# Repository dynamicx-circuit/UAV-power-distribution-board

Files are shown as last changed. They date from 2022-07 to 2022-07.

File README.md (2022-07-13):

#### 这是一个通过24V电池二串三并提高到48V的分电板
该版本采用LM5050-2作为理想二极管控制器以防止电池间互充。
#### 现存问题
1.现在无人机使用的为第5版，板上的48V降24V并未投入使用。<br>
2.使用该板时应注意电池的电压尽量保持一致，持续工作时间应小于10min，以避免电池过热。<br>
3.实机测试时MOS管需安装散热片并配合散热风扇使用，以免MOS热击穿。<br>
4.若要进行实机测试，***一定要在48V输出和GDN之间接入气体放电管***，并且***切记不可在48V输出和GND之间接入压敏电阻***。（接入压敏电阻后在限流情况下，输出电压较输入电压低2V~3V，未限流情况下，压敏电阻会在接GND的一侧炸裂，目前原因不明。）<br>
5.尽量使用高温锡焊接。<br>
6.该版本的地回路并未进行开窗，输出地较电池负极端距离较远。<br>

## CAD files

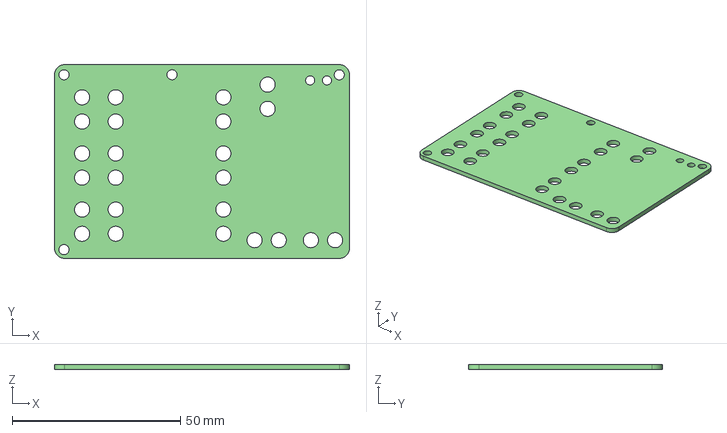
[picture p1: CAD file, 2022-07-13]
无人机分电板_V5.step
87.8 x 57.7 x 1.60 mm

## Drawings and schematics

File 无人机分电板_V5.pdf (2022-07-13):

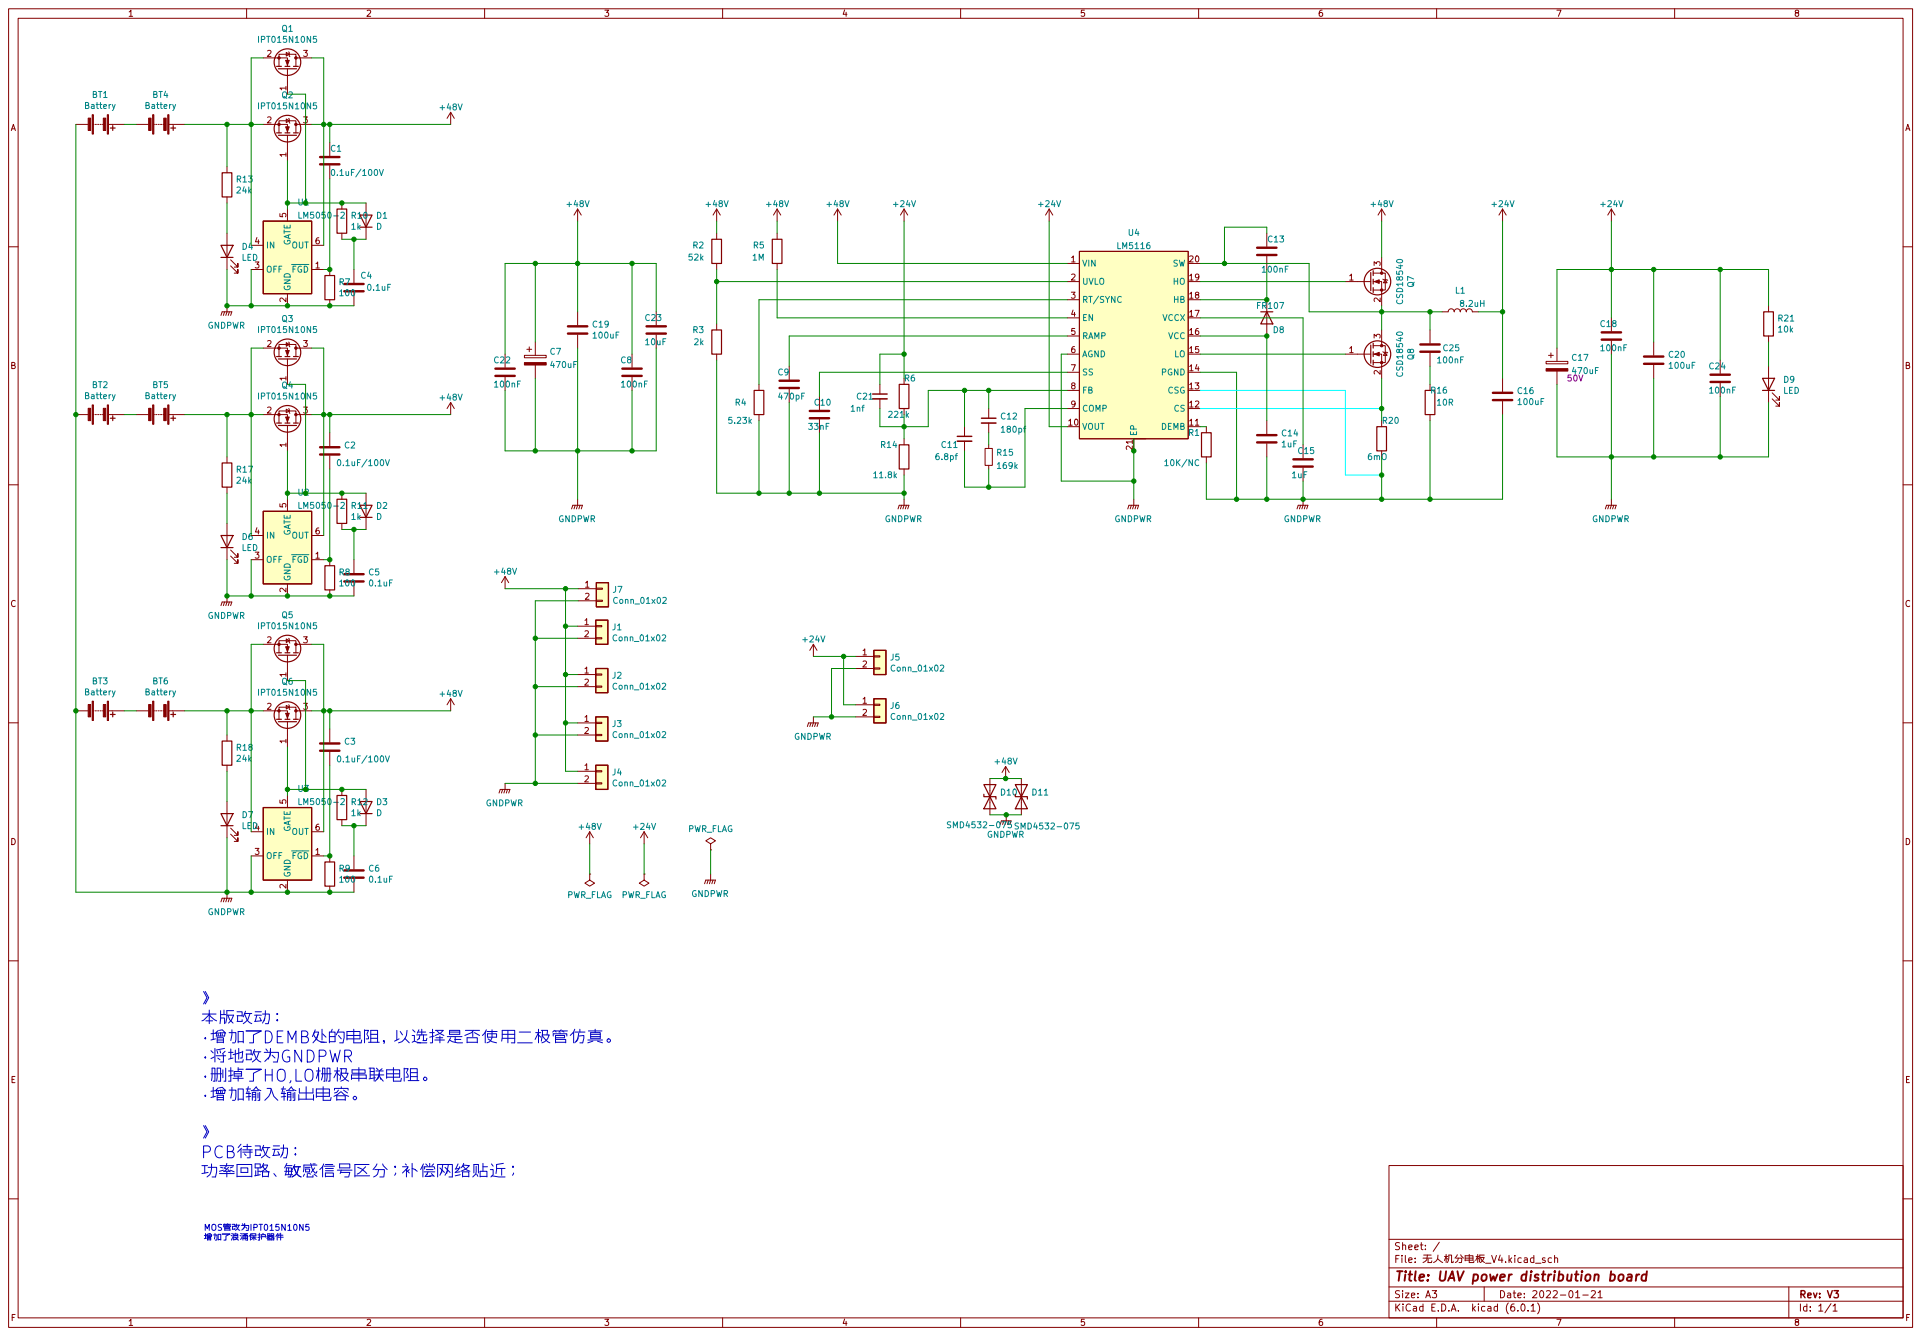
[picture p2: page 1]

þÿg,rHe9R¨ÿ
þÿ·XžR N†DEMBYv„u5–;ÿNå• béf/T&O•u(NŒg•{¡Nÿw0-
þÿ·XžR •“Qe•“Qúu5[¹0-

þÿRŸs‡VÞ•ï0eOaOáS÷S:RÿˆeP••Q~Ü•4•Ñÿ

þÿFile: eàNºg:Ru5g•_V4.kicad_sch Sheet: /
Id: 1/1 Title: UAV power distribution board

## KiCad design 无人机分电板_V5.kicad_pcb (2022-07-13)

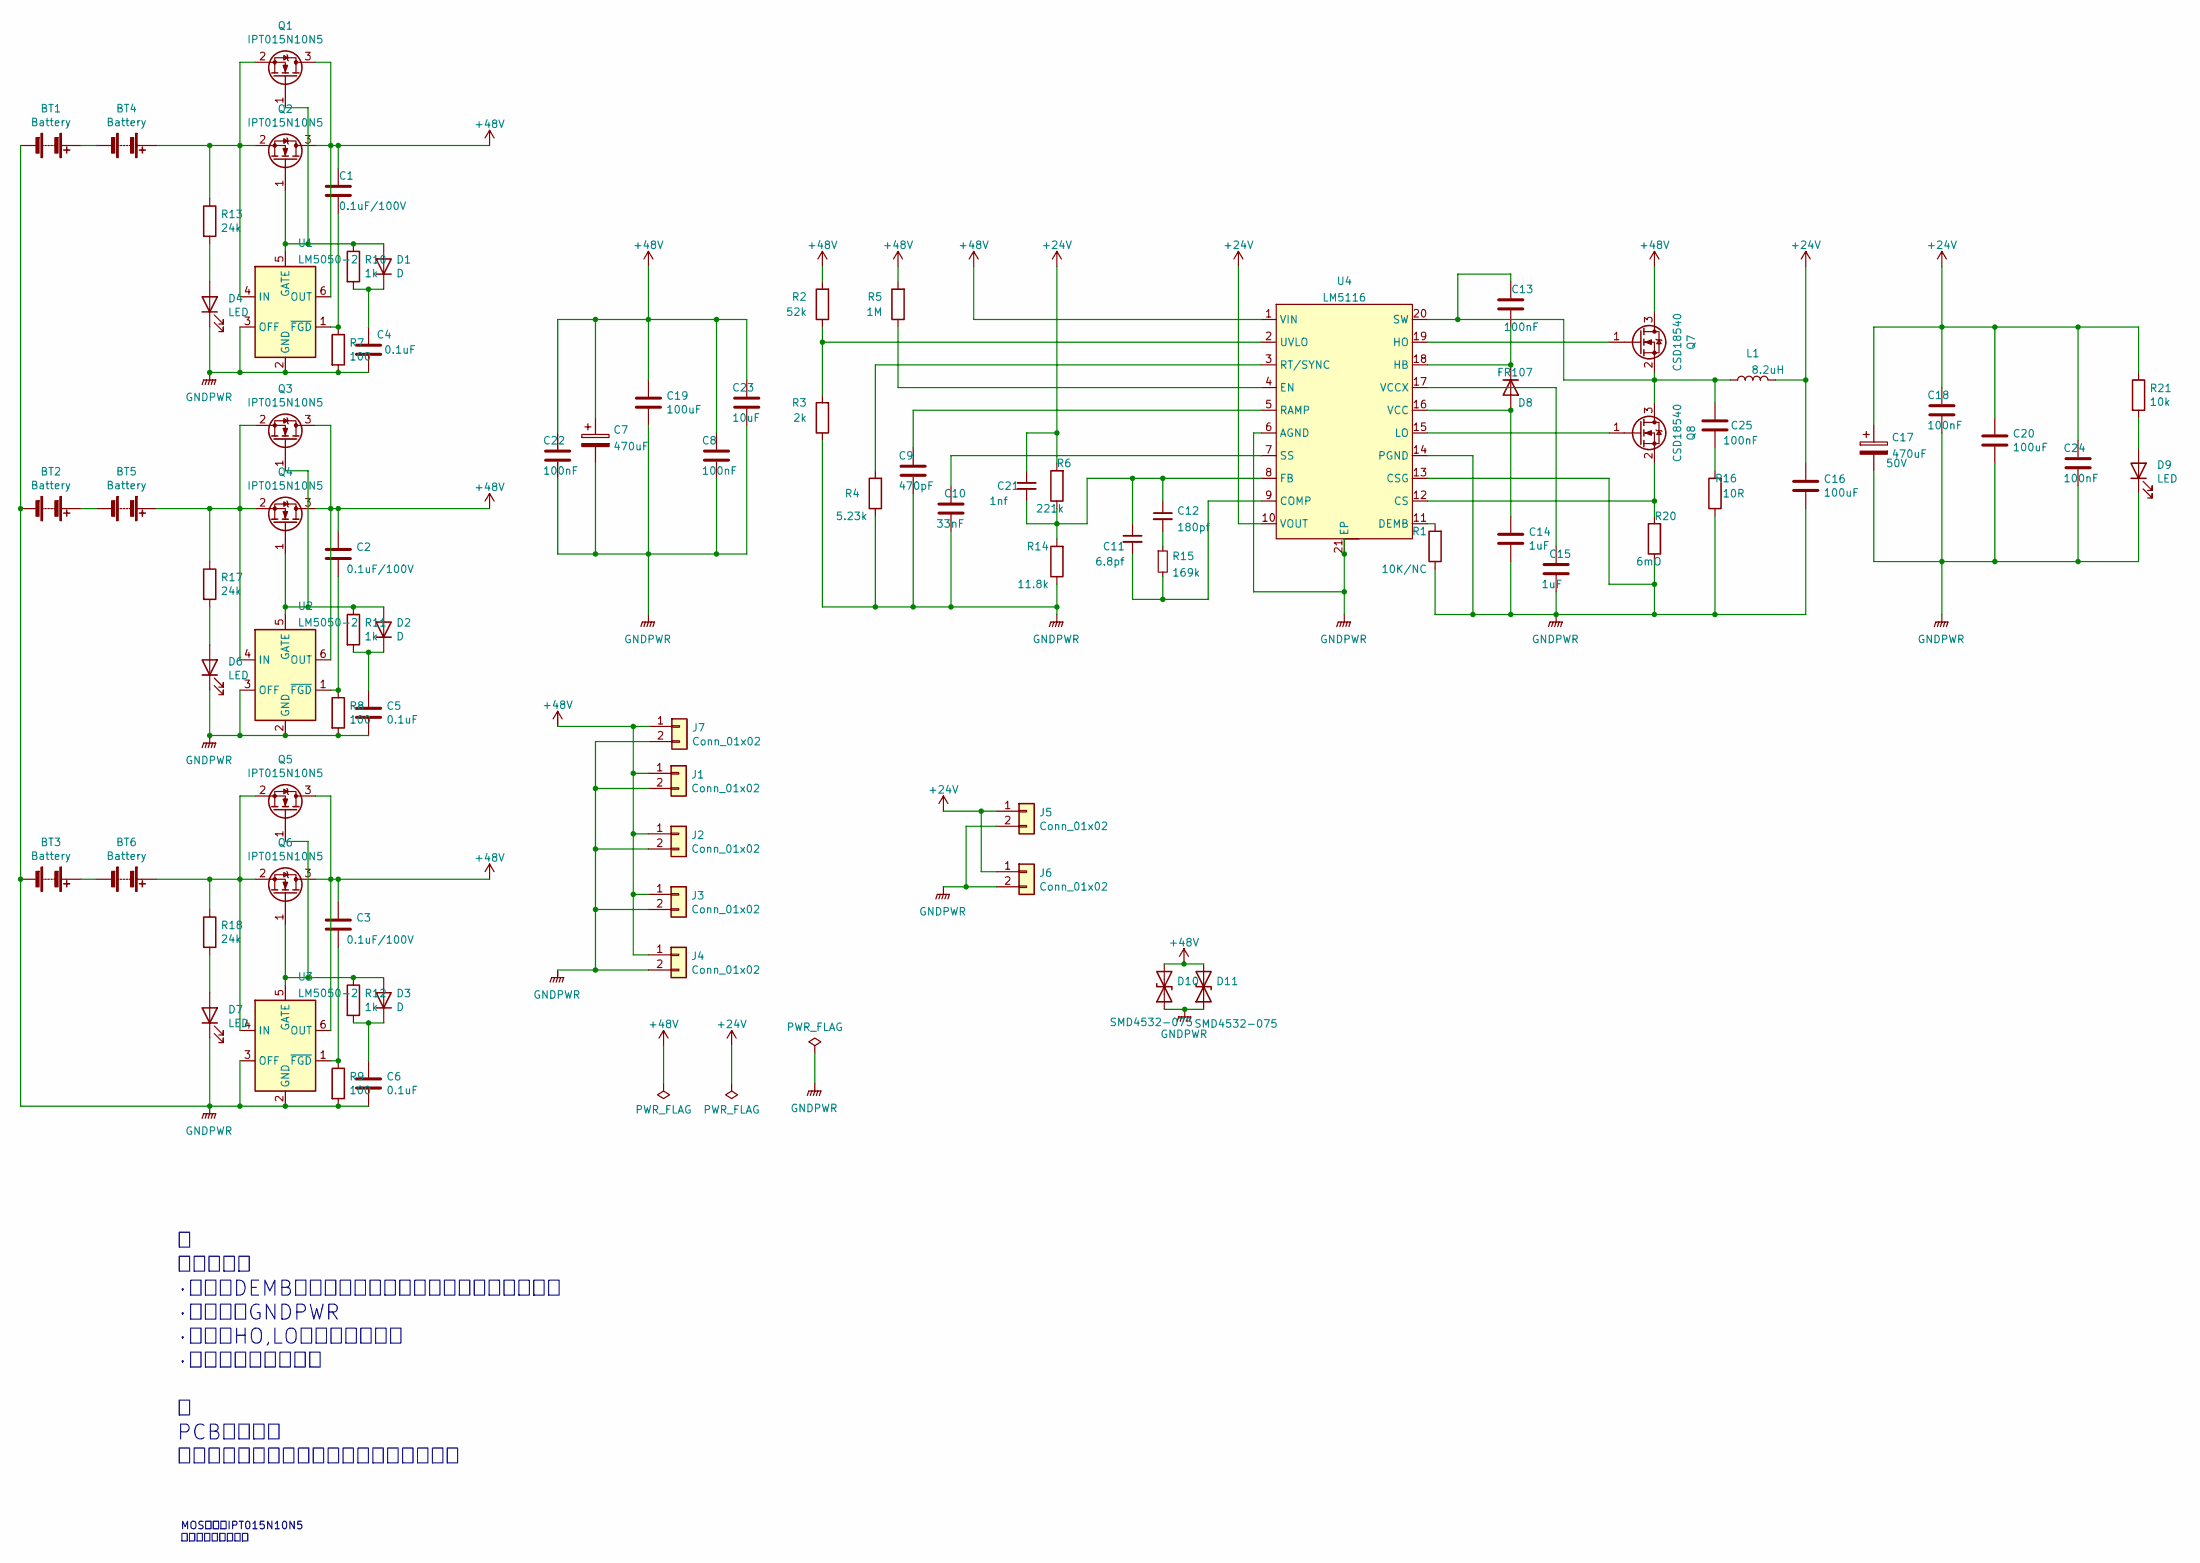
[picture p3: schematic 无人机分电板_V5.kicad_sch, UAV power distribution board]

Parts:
BT1, BT2, BT3, BT4, BT5, BT6: Battery; AMASS_XT60-M_1x02_P7.20mm_Vertical
C1, C2, C3: 0.1uF/100V; C_0603_1608Metric_Pad1.08x0.95mm_HandSolder
C4, C5, C6: 0.1uF; C_0603_1608Metric_Pad1.08x0.95mm_HandSolder
C7, C17: 470uF; CP_Elec_6.3x7.7
C8, C13, C18, C25: 100nF; C_0603_1608Metric_Pad1.08x0.95mm_HandSolder
C9: 470pF; C_0603_1608Metric_Pad1.08x0.95mm_HandSolder
C10: 33nF; C_0603_1608Metric_Pad1.08x0.95mm_HandSolder
C11: 6.8pf; C_0603_1608Metric_Pad1.08x0.95mm_HandSolder
C12: 180pf; C_0603_1608Metric_Pad1.08x0.95mm_HandSolder
C14, C15: 1uF; C_0603_1608Metric_Pad1.08x0.95mm_HandSolder
C16, C19, C20: 100uF; C_0805_2012Metric_Pad1.18x1.45mm_HandSolder
C21: 1nf; C_0603_1608Metric_Pad1.08x0.95mm_HandSolder
C22, C24: 100nF; C_0402_1005Metric_Pad0.74x0.62mm_HandSolder
C23: 10uF; C_0603_1608Metric_Pad1.08x0.95mm_HandSolder
D1, D2, D3: D; D_SOD-123
D4, D6, D7, D9: LED; LED_0603_1608Metric_Pad1.05x0.95mm_HandSolder
D8: FR107; D_SOD-123
D10, D11: SMD4532-075; D_1812_4532Metric_Pad1.30x3.40mm_HandSolder
J1, J2, J3, J4, J5, J6: Conn_01x02; AMASS_XT60-F_1x02_P7.20mm_Vertical
J7: Conn_01x02; AMASS_XT30U-F_1x02_P5.0mm_Vertical
L1: 8.2uH; L_Wuerth_HCI-1365
Q1, Q2, Q3, Q4, Q5, Q6: IPT015N10N5; Infineon_PG-HSOF-8-1
Q7, Q8: CSD18540; VSONP-8-1EP_5x6_P1.27mm
R1: 10K/NC; R_0603_1608Metric_Pad0.98x0.95mm_HandSolder
R2: 52k; R_0603_1608Metric_Pad0.98x0.95mm_HandSolder
R3: 2k; R_0603_1608Metric_Pad0.98x0.95mm_HandSolder
R4: 5.23k; R_0603_1608Metric_Pad0.98x0.95mm_HandSolder
R5: 1M; R_0603_1608Metric_Pad0.98x0.95mm_HandSolder
R6: 221k; R_0603_1608Metric_Pad0.98x0.95mm_HandSolder
R7, R8, R9: 100; R_0603_1608Metric_Pad0.98x0.95mm_HandSolder
R10, R11, R12: 1k; R_0603_1608Metric_Pad0.98x0.95mm_HandSolder
R13, R17, R18: 24k; R_0603_1608Metric_Pad0.98x0.95mm_HandSolder
R14: 11.8k; R_0603_1608Metric_Pad0.98x0.95mm_HandSolder
R15: 169k; R_0603_1608Metric_Pad0.98x0.95mm_HandSolder
R16: 10R; R_0603_1608Metric_Pad0.98x0.95mm_HandSolder
R20: 6mO; R_2010_5025Metric_Pad1.40x2.65mm_HandSolder
R21: 10k; R_0603_1608Metric_Pad0.98x0.95mm_HandSolder
U1, U2, U3: LM5050-2; TSOT-23-6
U4: LM5116; HTSSOP-20-1EP_4.4x6.5mm_P0.65mm_EP2.85x4mm

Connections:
+24V: C16.1, C17.1, C18.1, C20.1, C21.1, C24.1, J5.1, J6.1, L1.2, R6.2, R21.1, U4.10 (VOUT)
+48V: C1.1, C2.1, C3.1, C7.1, C8.1, C19.1, C22.1, C23.1, D10.2 (A2), D11.2 (A2), J1.1, J2.1, J3.1, J4.1, J7.1, Q1.3 (D), Q2.3 (D), Q3.3 (D), Q4.3 (D), Q5.3 (D), Q6.3 (D), Q7.3 (D), R2.2, R5.2, U1.6 (OUT), U2.6 (OUT), U3.6 (OUT), U4.1 (VIN); also elsewhere on the board
GNDPWR: BT1.2 (-), BT2.2 (-), BT3.2 (-), C4.2, C5.2, C6.2, C7.2, C8.2, C9.2, C10.2, C14.2, C15.2, C16.2, C17.2, C18.2, C19.2, C20.2, C22.2, C23.2, C24.2, D4.1 (K), D6.1 (K), D7.1 (K), D9.1 (K), D10.1 (A1), D11.1 (A1), J1.2, J2.2, J3.2, J4.2, J5.2, J6.2, J7.2, R1.1, R3.1, R4.1, R7.2, R8.2, R9.2, R14.1, R16.1, R20.1, U1.2 (GND), U1.3 (OFF), U2.2 (GND), U2.3 (OFF), U3.2 (GND), U3.3 (OFF), U4., U4.6 (AGND), U4.13 (CSG), U4.14 (PGND), U4.21 (EP); also elsewhere on the board
unnamed: BT1.1 (+), BT4.2 (-)
unnamed: BT2.1 (+), BT5.2 (-)
unnamed: BT3.1 (+), BT6.2 (-)
unnamed: BT4.1 (+), Q1.2 (S), Q2.2 (S), R13.1, U1.4 (IN)
unnamed: BT5.1 (+), Q3.2 (S), Q4.2 (S), R17.1, U2.4 (IN)
unnamed: BT6.1 (+), Q5.2 (S), Q6.2 (S), R18.1, U3.4 (IN)
unnamed: C1.2, R7.1, U1.1 (~FGD)
unnamed: C2.2, R8.1, U2.1 (~FGD)
unnamed: C3.2, R9.1, U3.1 (~FGD)
unnamed: C4.1, D1.1 (K), R10.2
unnamed: C5.1, D2.1 (K), R11.2
unnamed: C6.1, D3.1 (K), R12.2
unnamed: C9.1, U4.5 (RAMP)
unnamed: C10.1, U4.7 (SS)
unnamed: C11.1, C12.1, C21.2, R6.1, R14.2, U4.8 (FB)
unnamed: C11.2, R15.2, U4.9 (COMP)
unnamed: C12.2, R15.1
unnamed: C13.1, C25.1, L1.1, Q7.2 (S), Q8.3 (D), U4.20 (SW)
unnamed: C13.2, D8.1 (K), U4.18 (HB)
unnamed: C14.1, D8.2 (A), U4.16 (VCC)
unnamed: C15.1, U4.17 (VCCX)
unnamed: C25.2, R16.2
unnamed: D1.2 (A), Q1.1 (G), Q2.1 (G), R10.1, U1.5 (GATE)
unnamed: D2.2 (A), Q3.1 (G), Q4.1 (G), R11.1, U2.5 (GATE)
unnamed: D3.2 (A), Q5.1 (G), Q6.1 (G), R12.1, U3.5 (GATE)
unnamed: D4.2 (A), R13.2
unnamed: D6.2 (A), R17.2
unnamed: D7.2 (A), R18.2
unnamed: D9.2 (A), R21.2
unnamed: Q7.1 (G), U4.19 (HO)
unnamed: Q8.1 (G), U4.15 (LO)
unnamed: Q8.2 (S), R20.2, U4.12 (CS)
unnamed: R1.2, U4.11 (DEMB)
unnamed: R2.1, R3.2, U4.2 (UVLO)
unnamed: R4.2, U4.3 (RT/SYNC)
unnamed: R5.1, U4.4 (EN)

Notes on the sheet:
》 本版改动： ·增加了DEMB处的电阻，以选择是否使用二极管仿真。 ·将地改为GNDPWR ·删掉了HO,LO栅极串联电阻。 ·增加输入输出电容。 》 PCB待改动： 功率回路、敏感信号区分；补偿网络贴近；
MOS管改为IPT015N10N5 增加了浪涌保护器件

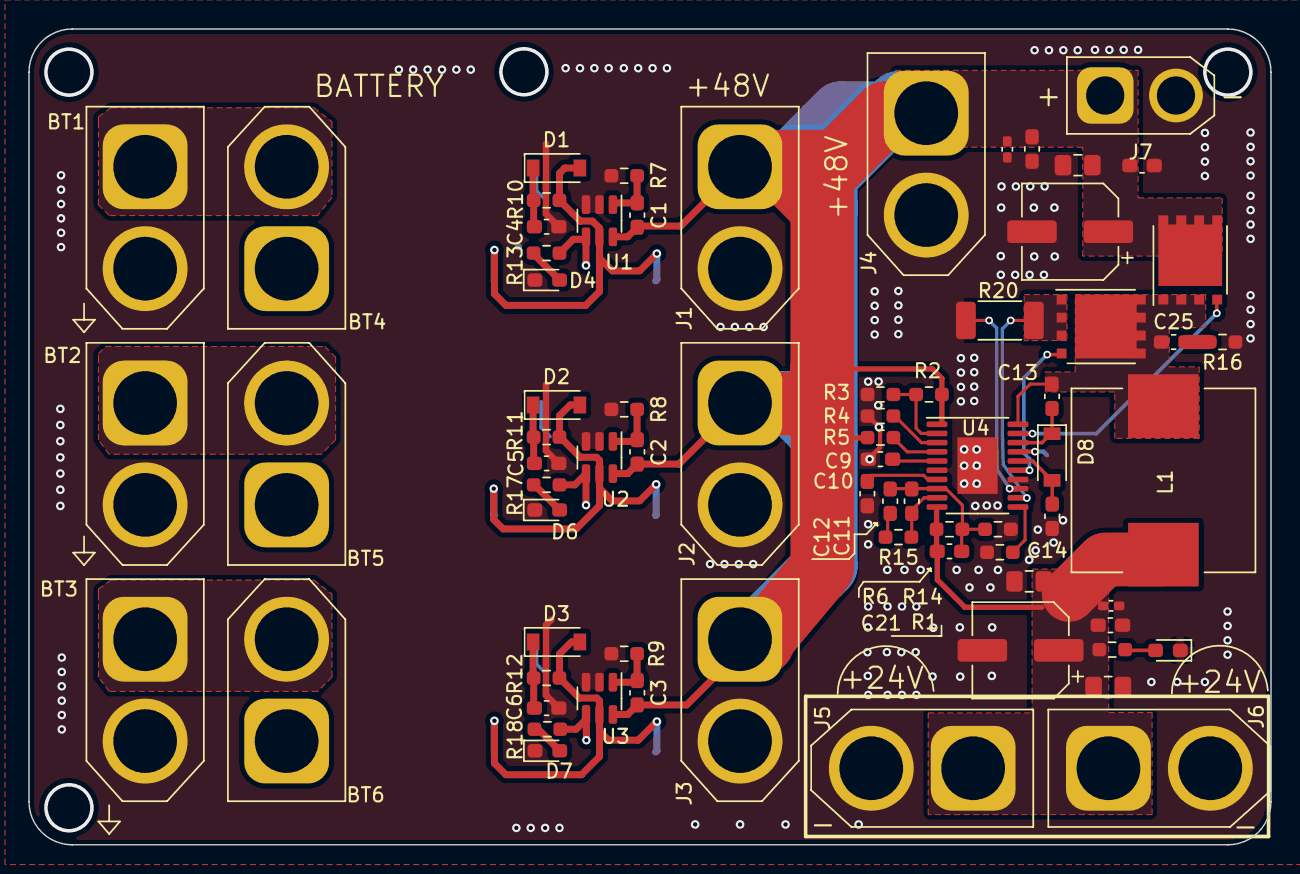
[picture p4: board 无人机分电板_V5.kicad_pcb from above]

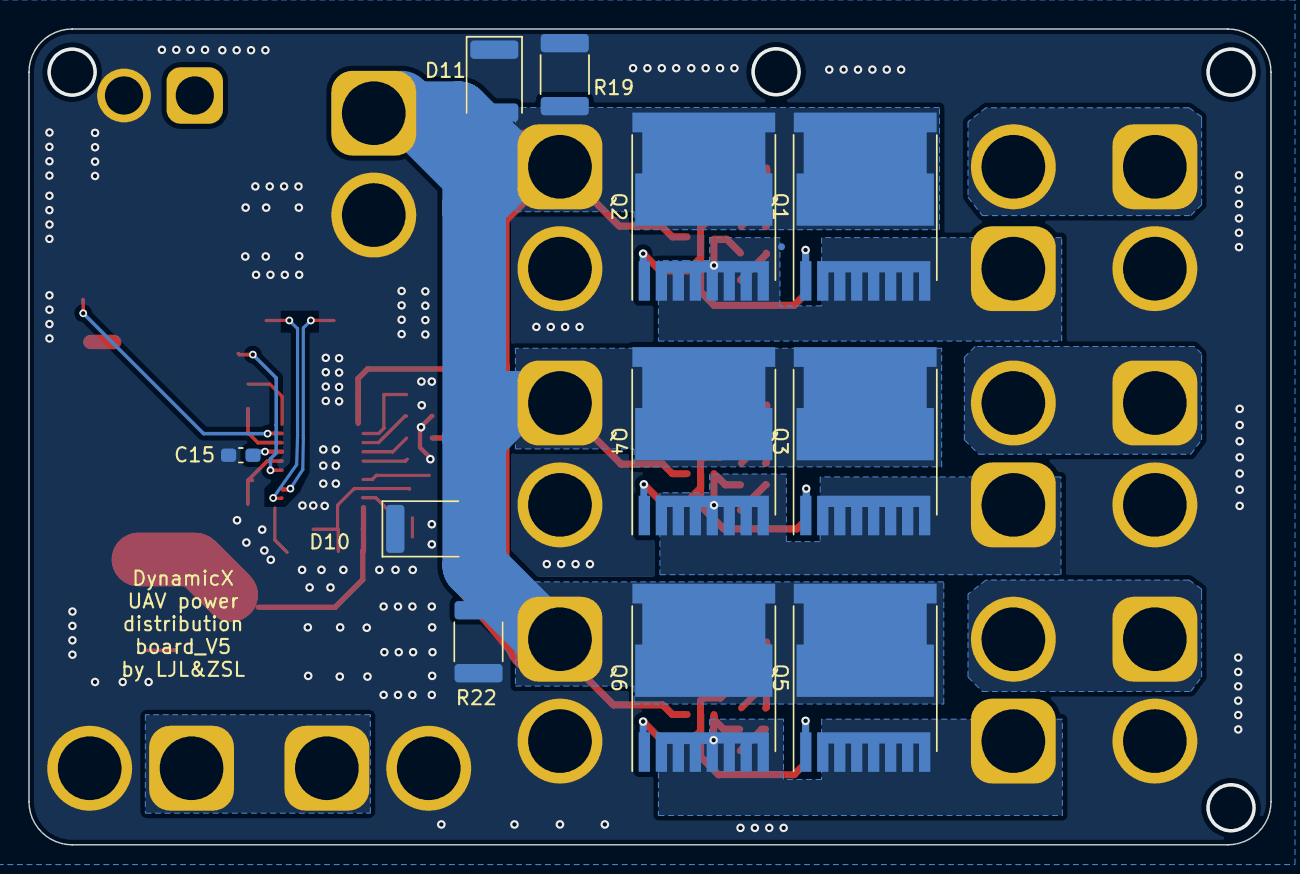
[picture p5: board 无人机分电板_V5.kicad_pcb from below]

Board: 2 copper layers, 87.8 x 57.7 mm, 83 parts (11 on the bottom side), 39 nets.

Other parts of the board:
R19, R22: Varistor_82V; R_1812_4532Metric_Pad1.30x3.40mm_HandSolder

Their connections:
+48V: R19.1, R22.1; also elsewhere on the board
GNDPWR: R19.2, R22.2; also elsewhere on the board
